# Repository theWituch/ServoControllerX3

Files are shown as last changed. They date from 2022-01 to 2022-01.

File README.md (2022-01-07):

# SCX3
3 Axis **Open-Loop STEP/DIR Position Control** to **Closed-Loop +/-10V Speed Control** Interface

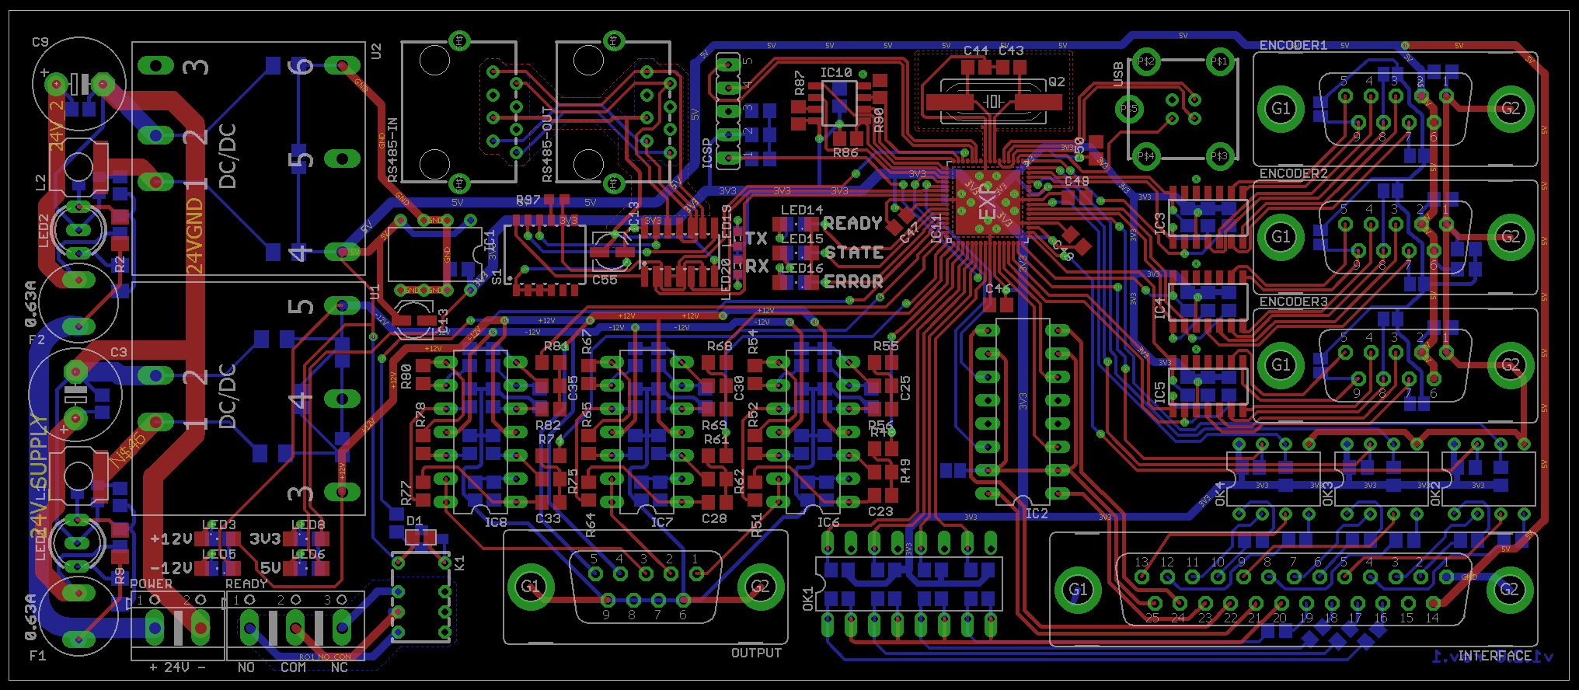
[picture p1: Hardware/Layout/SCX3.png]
PCB


## About
The system is an interface between two systemically incompatible types of control - open loop STEP/DIR in which there is no feedback, because it is open, and closed loop +/- 10V in which the DIRECT feedback is in the form of the axis position from a linear encoder for a linear axis or rotary for rotary axes (e.g. rotary table).

## How it works

The open-loop CNC controller has no coupling, it only sends STEP/DIR signals and waits for the movement to be performed, e.g. by a stepper motor or servo drive with a STEP / DIR input. This solution is nice and cheap, but it brings with it problems such as the lack of feedback on whether the move was actually made.

Of course, it is possible to detect, for example, in self-drives, the lack of rotation of the motor shaft, but the rotation of the motor does not have to mean the axis shift (failure).

In addition, the entire kinematic chain, which has its efficiency, causes that the positioning from the motor axis is not accurately reflected at the end of the chain (on the machine table).

## Project assumptions

The assumptions for the system were such as to:
* fit on one board for three axes of the machine
* reduce noise on the analog outputs +/- 10V
* ensure internal distribution of the necessary voltages for the system (uC, outputs +/- 10V) and connected encoders from the power supply 12-24VDC
* add a readiness relay (not a safe output, only OK status signaling, as in the servers it was supposed to cooperate with)
* increase the uC computing power
* increase the capacity of the encoder inputs
* integrate the RS232 interface in the system
* and adjust the shape of the board to the format that allows it to be reasonably mounted, e.g. on a DIN rail.

## Progress

The project, due to the fact that while writing the firmware, I encountered a bug with the EEPROM memory built into the uC, it got stuck for a good two years.

Problem: https://www.microchip.com/forums/m1043135.aspx  
Solution: https://www.microchip.com/forums/FindPost/1064146

## Versions

See version description to get more detailed informations.

* [version 1.2.0](V1.2.0.md)
* [version 1.1.0](V1.1.0.md)
* [version 1.0.0](V1.0.0.md)

## License

Whole SCX3 project follow [CC-BY-NC-SA-4.0 license](https://creativecommons.org/licenses/by-nc-sa/4.0/). Thus, project is freely available for academic purpose or individual research, but restricted for commecial use.

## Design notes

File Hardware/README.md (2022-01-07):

# SCX3 Hardware
3 Axis **Open-Loop STEP/DIR Position Control** to **Closed-Loop +/-10V Speed Control** Interface - Hardware

## About

The hardware for the SCX3 controller was developed using the EAGLE 7.7.0 environment.

## Status

The project has not been developed for a long time and the content of the repository has not been checked. Therefore, there is no guarantee that the project files will generate a PCB without any additional steps.

Additionally, this hardware version (1.2.0) has not been tested on the built prototype.

The only version tested on a prototype is 1.0.0 - which contained bugs that were fixed in later versions.

## License

SCX3 Hardware follow [CC-BY-NC-SA-4.0 license](LICENSE). Thus, those compounds are freely available for academic purpose or individual research, but restricted for commecial use.

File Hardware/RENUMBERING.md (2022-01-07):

# Don't renumber these!

POWER;READY;INTERFACE;ENCODER;OUTPUT;RS232;USB;ICSP

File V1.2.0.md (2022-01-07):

# SCX3 v1.2.0

## Layout

PCB

## Hardware changes

The most important hardware change is the addition of an RS-485 interface with two RJ-45 connectors instead of the RS-232 interface. RS-485 has better properties allowing it to work in more difficult conditions. The parameters of the RS-485 interface can be hardware controlled by means of S1 switches.

The entire power section was also rebuilt by changing the +/- 12V converter from Traco to Aimtec. The converters now have individual 24V power circuits with a separate fuse and a LED indicator for the burnout status.

## Firmware changes

The software has undergone general cleanup. The layout of the program has been changed, although its functionality has remained almost completely unchanged.

The most important change was the implementation of the MODBUS protocol which replaced text communication over RS-232.

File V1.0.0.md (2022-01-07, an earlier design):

# SCX3 v1.0.0

First version of board, with working prototype built.

## Layout

PCB

## Layout elements

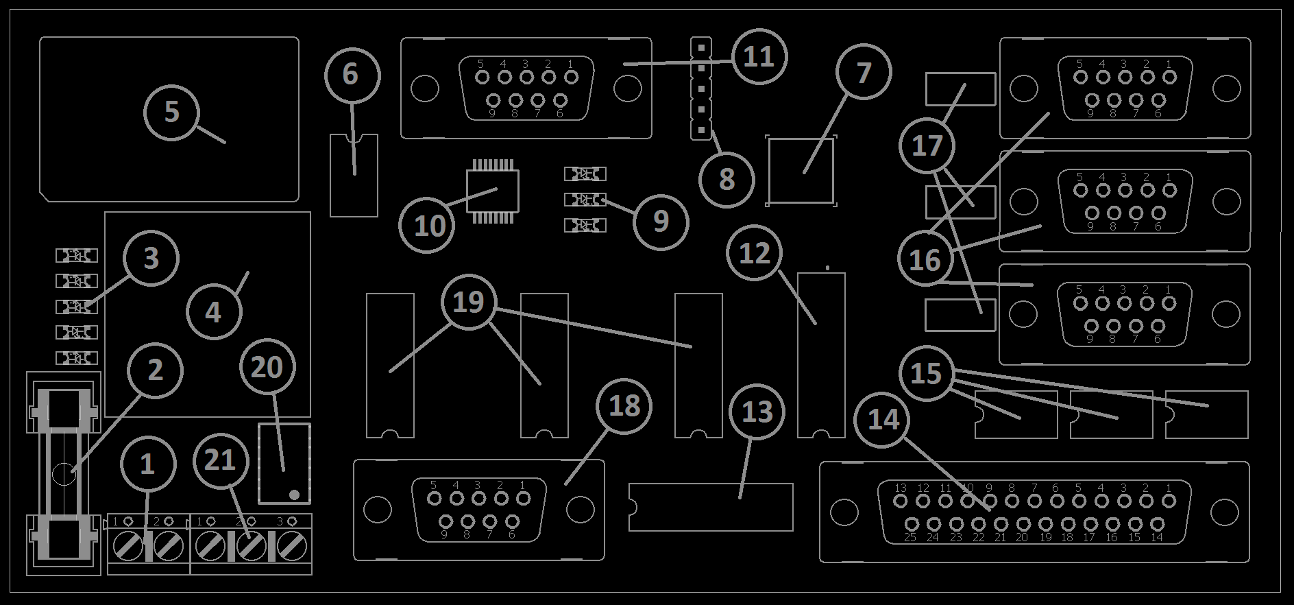
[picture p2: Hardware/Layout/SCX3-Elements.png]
PCB elements


     1 - 12-24 VDC power connector (+ VDC, GND)
     2 - fuse socket
     3 - 12-24VDC, +/- 12VDC, 5VDC, 3V3DC voltage presence LEDs
     4 - DC / DC converter 12-24VDC to 5VDC
     5 - DC / DC converter 12-24VDC to +/- 12VDC
     6 - LDO 5VDC to 3V3DC stabilizer
     7 - PIC32 microcontroller
     8 - ICSP connector for programming the microcontroller
     9 - device status indicator LEDs
    10 - RS232 transceiver
    11 - DB9 RS232 connector
    12 - DO transistorized digital output driver
    13 - DI digital input optocouplers
    14 - DB25 interface for STEP / DIR, DI, DO "INTERFACE" signals
    15 - STEP / DIR input optocouplers
    16 - DB9 connectors for encoder inputs "ENCODER (1,2,3)"
    17 - optocouplers for encoder inputs
    18 - DB9 "OUTPUT" connector of symmetrical +/- 10VDC outputs
    19 - symmetrical +/- 10VDC operational amplifiers
    20 - "READY" system readiness circuit relay
    21 - 3-pin connector of the "READY" relay (NO, COM, NC contacts)

## Prototype

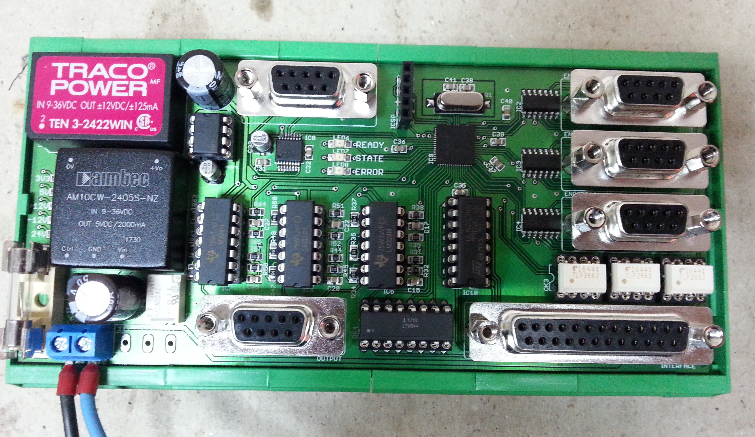
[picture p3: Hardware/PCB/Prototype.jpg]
PCB prototype

*There are no '21' connector soldered.*

The prototype showed design errors (wrongly arranged descriptions, swapped pin in the ENCODER1 encoder plug and badly designed READY relay power supply). However, this was not an obstacle to testing and developing the firmware.

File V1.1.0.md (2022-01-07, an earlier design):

# SCX3 v1.1.0

First version of board, with working prototype built.

## Layout

PCB

## Hardware changes

- External SPI EEPROM memory added
- K1 (READY) relay has been changed to 5V supply type due to separation of ground from supply voltage.
- RS232 interface socket has been changed from DB9 plug to RJ9
- The +/- 12V voltage lead has been added to the OUTPUT connector

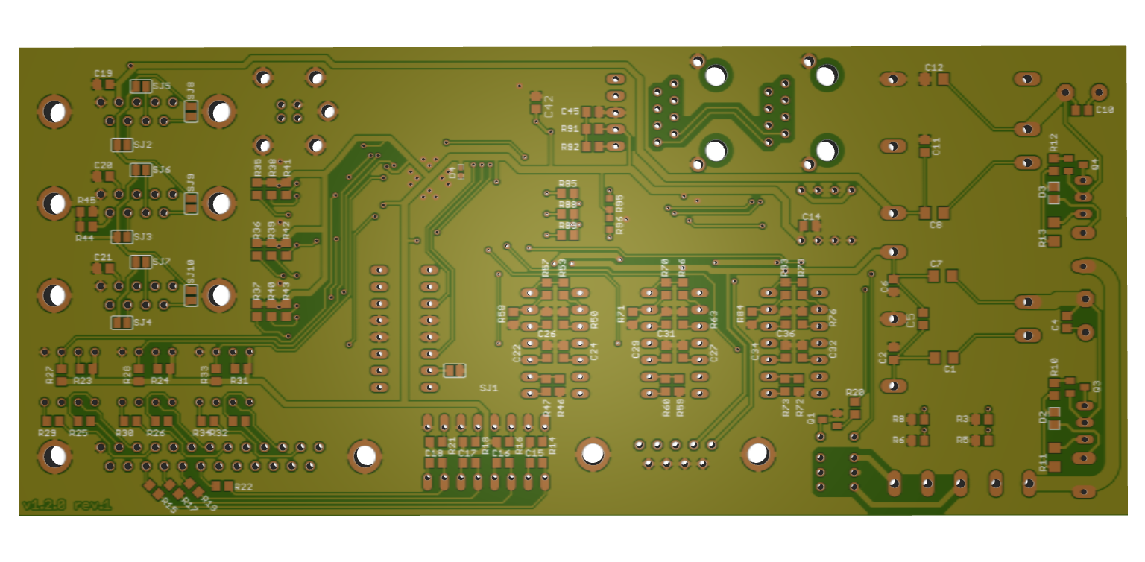
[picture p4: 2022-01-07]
Hardware/Layout/SCX3-3D_Bottom.png

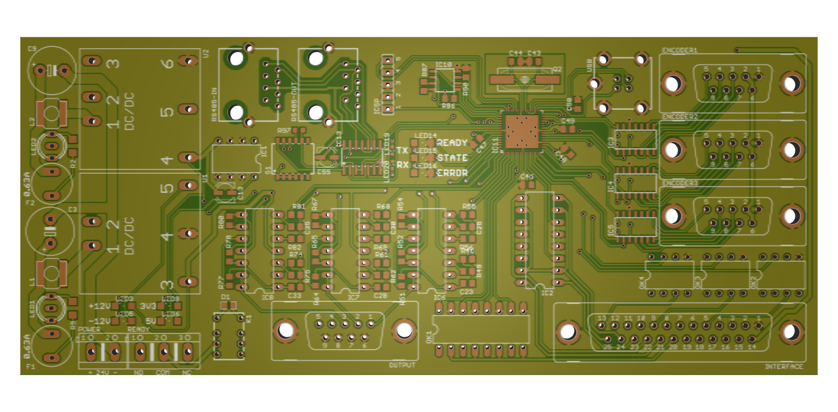
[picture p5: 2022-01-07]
Hardware/Layout/SCX3-3D_Top.png

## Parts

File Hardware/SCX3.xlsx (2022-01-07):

NO | Qty | Device | Value | Package | Parts | Description | POSIADANE | ZAMOWIENIE
1 | 1 | 1N4148SMD-0805 | 1N4148SMD-0805 | D0805 | D1 | DIODE
2 | 1 | AK500/2 | 12/24V_CON | AK500/2 | POWER | CONNECTOR
3 | 1 | AK500/3 | READY | AK500/3 | READY | CONNECTOR
4 | 1 | AM10CW-2405S-NZ | AM10CW-2405S-NZ | AM10CW-NZ | U1 | 10 Watt | 2A | DC-DC Converter
5 | 1 | BC848SMD | BC848SMD | SOT23 | Q4 | NPN Transistor
6 | 14 | C-EUC0805 | 100n | C0805 | C29, C30, C31, C32, C34, C35, C36, C37, C39, C40, C42, C43, C44, C45 | CAPACITOR
7 | 9 | C-EUC0805 | 33n | C0805 | C14, C16, C18, C19, C21, C23, C24, C26, C28 | CAPACITOR
8 | 6 | C-EUC0805 | 10n | C0805 | C15, C17, C20, C22, C25, C27 | CAPACITOR
9 | 5 | C-EUC0805 | 10uF | C0805 | C3, C10, C11, C12, C13 | CAPACITOR
10 | 2 | C-EUC0805 | 1nF/2KV | C0805 | C4, C8 | CAPACITOR
11 | 2 | C-EUC0805 | 27p | C0805 | C38, C41 | CAPACITOR
12 | 3 | C-EUC0805 | 1uF | C0805 | C2, C5, C7 | CAPACITOR
13 | 1 | CPOL-EUE5-10.5 | 200uF | E5-10,5 | C6 | POLARIZED CAPACITOR
14 | 1 | CPOL-EUE5-10.5 | 330uF | E5-10,5 | C1 | POLARIZED CAPACITOR
15 | 1 | CPOL-EUUD-4X5,8 | 100n | UD-4X5,8 | C33 | POLARIZED CAPACITOR
16 | 1 | CPOL-EUUD-4X5,8 | 10uF | UD-4X5,8 | C9 | POLARIZED CAPACITOR
17 | 1 | CRYSTALSM49 | 20MHz 18pF | SM49 | Q1 | CRYSTAL
18 | 1 | DJNR6028--S | 4,7uH | DJNR6028 | L1 | INDUCTOR
19 | 5 | F09VP |  | F09VP | ENCODER1, ENCODER2, ENCODER3, OUTPUT, RS-232 | SUB-D
20 | 1 | F25VP |  | F25VP | INTERFACE | SUB-D
21 | 1 | G6K-2P-Y | G6K-2P-Y | G6K-2P-Y | K1 | Low Signal Relay
22 | 1 | JP5E | ICSP | JP5 | ICSP | JUMPER
23 | 3 | LEDSML1206 | LED +12V, -12V, 5V | SML1206 | LED2, LED3, LED4 | Green LED 20mA 2,5V
24 | 3 | LEDSML1206 | LED 24V, 3V3, READY | SML1206 | LED1, LED5, LED6 | Green LED 10mA 2,5V
25 | 1 | LEDSML1206 | LED ERROR | SML1206 | LED8 | Red LED 10mA 2,5V
26 | 1 | LEDSML1206 | LED STATE | SML1206 | LED7 | Orange LED 10mA 2,5V
27 | 3 | LM324N | LM324N | DIL14 | IC5, IC6, IC7 | OP AMP
28 | 3 | LM339D | LM339D | SO14 | IC2, IC3, IC4 | Low Power Low Offset Voltage Quad Comparators
29 | 1 | LTV844 | LTV844 | DIL16 | OK4 | SHARP OPTO COUPLER
30 | 1 | MAX3221CAE | MAX3221CAE | SSOP16 | IC8 | RS-232 Transceivers with AutoShutdown
31 | 1 | MAX604 | MAX604 | DIL08 | IC1 | LDO VOLTAGE REGULATOR
32 | 1 | PIC32MK1024MCF064 | PIC32 | QFN64-9X9 | IC9 | PIC32 MICROCONTROLLER
33 | 21 | R-EU_R0805 | 22K | R0805 | R30, R31, R34, R35, R36, R38, R40, R43, R44, R47, R48, R49, R51, R53, R56, R57, R60, R61, R62, R64, R66 | RESISTOR
34 | 20 | R-EU_R0805 | 4K7 | R0805 | R6, R7, R10, R11, R14, R16, R18, R19, R20, R21, R22, R23, R24, R25, R26, R73, R77, R81, R82, R88 | RESISTOR
35 | 12 | R-EU_R0805 | 47K | R0805 | R29, R33, R37, R41, R42, R46, R50, R54, R55, R59, R63, R67 | RESISTOR
36 | 8 | R-EU_R0805 | 470 | R0805 | R2, R3, R8, R9, R12, R13, R15, R17 | RESISTOR
37 | 7 | R-EU_R0805 | 10K | R0805 | R32, R39, R45, R52, R58, R65, R71 | RESISTOR
38 | 6 | R-EU_R0805 | 1K | R0805 | R28, R72, R74, R79, R84, R89 | RESISTOR
39 | 4 | R-EU_R0805 | 100 | R0805 | R5, R68, R69, R70 | RESISTOR
40 | 1 | R-EU_R0805 | 130 | R0805 | R4 | RESISTOR
41 | 1 | R-EU_R0805 | 330 | R0805 | R27 | RESISTOR
42 | 1 | R-EU_R1206 | 2K2 | R1206 | R1 | RESISTOR
43 | 1 | SH22,5 | 3A | SH22,5 | F1 | FUSE HOLDER grid 22,5 mm
44 | 1 | TEN3-2422WIN | TEN3-2422WIN | TEN3-WIN | U2 | 3W | DC/DC Converter
45 | 3 | TLP2662F | TLP2662F | DIL08 | OK1, OK2, OK3 | 2 GATE FAST OPTO COUPLER
46 | 1 | ULN2074BN | ULN2074BN | DIL16 | IC10 | DRIVER ARRAY
47
48
49
50

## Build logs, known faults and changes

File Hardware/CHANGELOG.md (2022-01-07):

# 1.2.0
- the dimensions of the plate have been corrected to 159x73mm (from 157x72mm)
- PCB dimensions have been corrected to 170x73mm (from 159x72mm), adding one housing module
- IC3-5 and IC6-8 have been relocated
- individual voltage fuses for DC / DC converters have been added with LEDs indicating burnout
- the USB interface has been implemented
- RX / TX signaling diodes for communication have been added
- an RS-485 interface with two RJ-45 sockets was implemented instead of the RS-232
- changed the + -12V converter type from Traco to Aimtec
- a diode has been added to protect the 3V3 power supply against overvoltage

# 1.1.0
- the error of connecting the encoder interface ENCODER1 has been corrected - the connection of the CH1_QE_x leads has been changed:
CH1_QE_A> IC9.30
CH1_QE_B> IC9.33
CH1_QE_I> IC9.31
- fixed error of connecting (no ground) relay output RO1 - change to 5V power supply
- the resistance values of the resistors R27 and R28 have been changed
R27> 1K ohm
228> 470 ohms
- the bug with the description of the R27 and R28 resistors has been corrected
- added external SPI EEPROM memory
- RS232 interface socket has been changed from DB9 plug to RJ9
- the position of the 24 / + - 12V converter and accessories has been corrected
- the position of the 5 / 3.3V converter and accessories has been corrected
- the +/- 12V voltage lead has been added to the OUTPUT connector

# 1.0.0
- the first version of the layout

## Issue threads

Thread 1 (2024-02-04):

If use pwm10v it suport for Axis Mach3

artayasa, 2024-02-04:
Hi sir.
I interest with your project i have ac servo snayo denki 200v, with 2000ppr. It posoble to use ypur hardware and frimeware? I want to used mach3

theWituch, 2024-02-16:
Hi,
you are free to use this design for personal purposes if you do not intend to commercially offer this layout for sale.
The project is unfinished (firmware), so if you want it as it is, it will be difficult to make it work - anyway fell free to create PR with updates ;)

artayasa, 2024-02-16:
> Hi, you are free to use this design for personal purposes if you do not intend to commercially offer this layout for sale. The project is unfinished (firmware), so if you want it as it is, it will be difficult to make it work - anyway fell free to create PR with updates ;)

So it not suport for step/dir but closeloop with encorder 2000ppr??
And posible to make for stm32f401??

theWituch, 2024-02-22:
It support STEP/DIR input from controller (eg. Mach3) - also this board has capability to recieve command also by RS-485 port (need firmware development).

Its designed to recieve motion commands (especially STEP/DIR) and control closed-loop +/-10V  speed-control servo. Any TTL encoder supported (2000ppr will work excellent).

Read README for more informations.
But remember - project is unfinished ;)

artayasa, 2024-02-22:
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

This is for bldc/pmsm motor control right sir??

artayasa, 2024-07-18:
> It is as described: 3 Axis Open-Loop _STEP/DIR Position Control_ to Closed-Loop _+/-10V Speed Control_ **Interface**

So its mean posoble to used for cnc?? Because speed control?? And cnc is position control right??

theWituch, 2024-07-25:
Of course, it is designed primarily for use in CNC machines :)

I'm afraid you don't understand the purpose of SCX3. It is primarily a controller, not an motor driver like servo driver (not have a power amplifier). It must cooperate as interface between NC controller and motor driver.

Here is simple [diagram of major usage of SCX3](https://www.plantuml.com/plantuml/png/PP11Ru9048Nl-oicN1kgoAs7HeCqDH4nW4qJus4BMzm8EsHPxA7fV--mc0RBRU1xUU-3PMkuDbrTCTPUf6guvZKeB4Gh6l3cSyQO5hdXggm4fC6x3zyCe45jf09diyl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).

artayasa, 2024-07-25:
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

Owhh i got it now. Do u have idea for encorder actual position?? Must be linier encorder???
And if like that its mean any servo suport speed control 0-10v are posible right???
So i will planing to used any servo drive or vesc ( vesc suport speed control but as i know only 0-5v) it posible to make it 0-5v??

theWituch, 2024-08-06:
No, linear encoder is not neccesary but best - you can use any encoder which will be used as "real position" feedback.
In fact, the motor encoder can also be used to measure the real position, but the mechanical system of the axis introduces an error and then such positioning is worse by a few micrometers or more.

Yes, any servo which accept analog input as control signal will work with SCX3.

Yes, you can make it 5V in two ways - one is to change values   of the appropriate resistors of analog output block (its harder) and second is to limit the maximum value for output in the firmware (easier and you can change it anytime by reflashing).

And again, as I mentioned previously you can use motor encoder as position feedback (connecting to SCX ENDODERx inputs) but you must change it in firmware to properly process motor encoder signal to position (very rarely one ppr is exactly a linear movement like 1um or 1mm because of mechanical system).

artayasa, 2024-08-06:
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

Oke thank u i gotit now, but the chip hard to find on my country, i think it is a stm32f407

theWituch, 2024-08-08:
I think best will be chip with hardware support for quadrature encoder like STM32F767ZI

artayasa, 2024-08-08:
> I think STM32f407 chip will be good as long have a hardware support for quadrature encoder.

Yes they have quadature suport, it just upload your code to stm32f407???

theWituch, 2024-08-12:
No, its not that simple. Firmware is written with Microchip libraries and for PIC32 uC registers. STM is quite different, so it must be adjusted. General firmware flow will work probably, but I didnt check how much work it needs.
And dont forget, the board must be changed too because STM32F407 has different package and pinout.

artayasa, 2024-08-13:
> No, its not that simple. Firmware is written with Microchip libraries and for PIC32 uC registers. STM is quite different, so it must be adjusted. General firmware flow will work probably, but I didnt check how much work it needs. And dont forget, the board must be changed too because STM32F407 has different package and pinout.

Oke sir, first must loking for pic32

theWituch, 2024-08-13:
Im not familiar with whole PIC32 family, so dont know. Just use PIC32MK1024MCF064 and you are ready to go with testing.
Which version of SCX3 you would use? I reccomend to start with latest [1.2.0](https://github.com/theWituch/ServoControllerX3/blob/master/V1.2.0.md)

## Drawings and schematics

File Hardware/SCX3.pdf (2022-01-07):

24V_2 | + + | +
Arkusz: 1/7 ABCD | 1 | 2 | 3 | 4 | 5 | 6 | ABCD 1 | 2 | 3 | 4 | 5 | 6

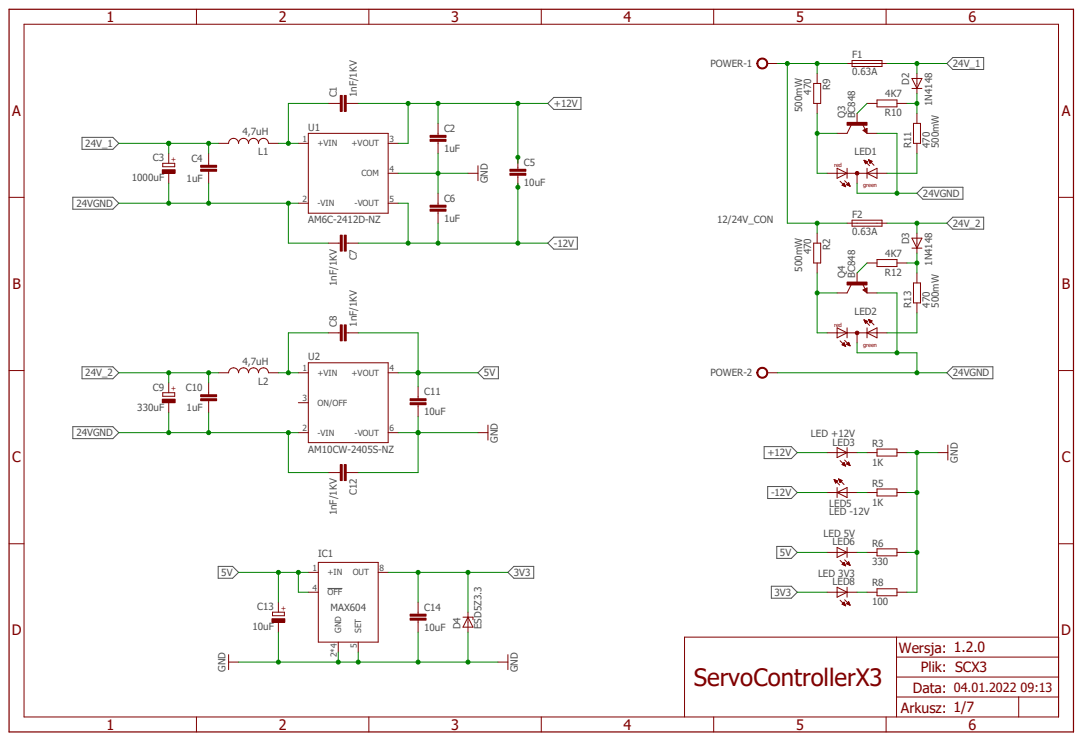
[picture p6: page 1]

# GND ⁴K7

Arkusz: 2/7 ABCD | 1 | 2 | 3 | 4 | 5 | 6 | ABCD 1 | 2 | 3 | 4 | 5 | 6

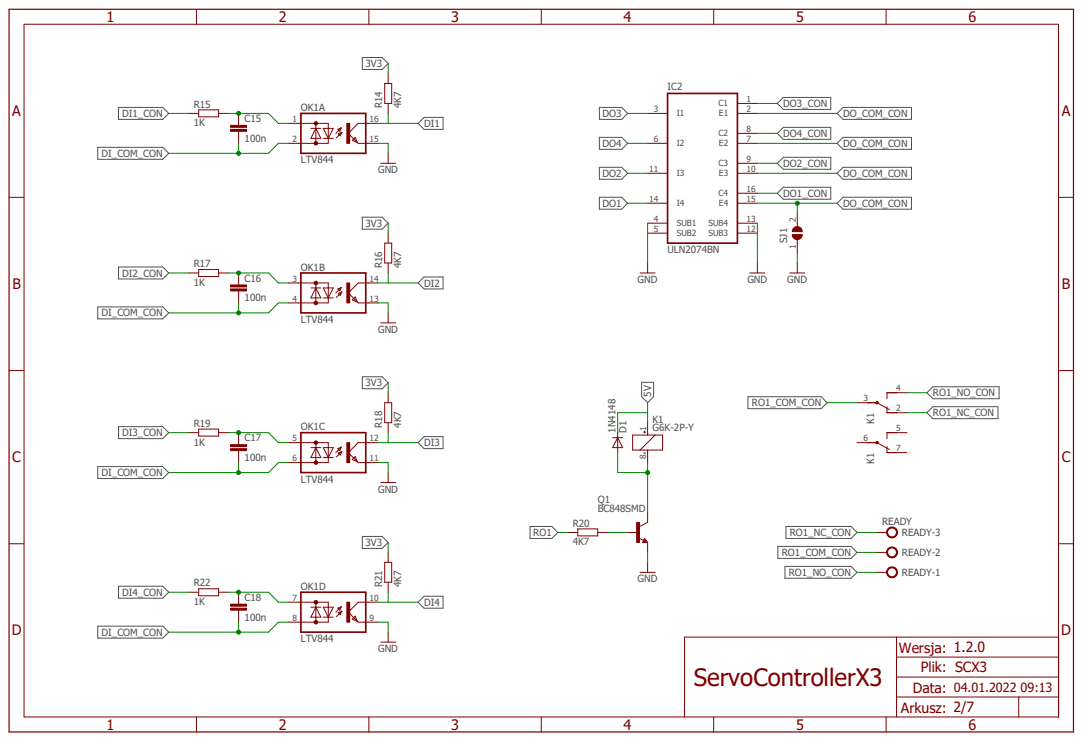
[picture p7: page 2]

Arkusz: 3/7 ABCD | 1 | 2 | 3 | 4 | 5 | 6 | ABCD 1 | 2 | 3 | 4 | 5 | 6

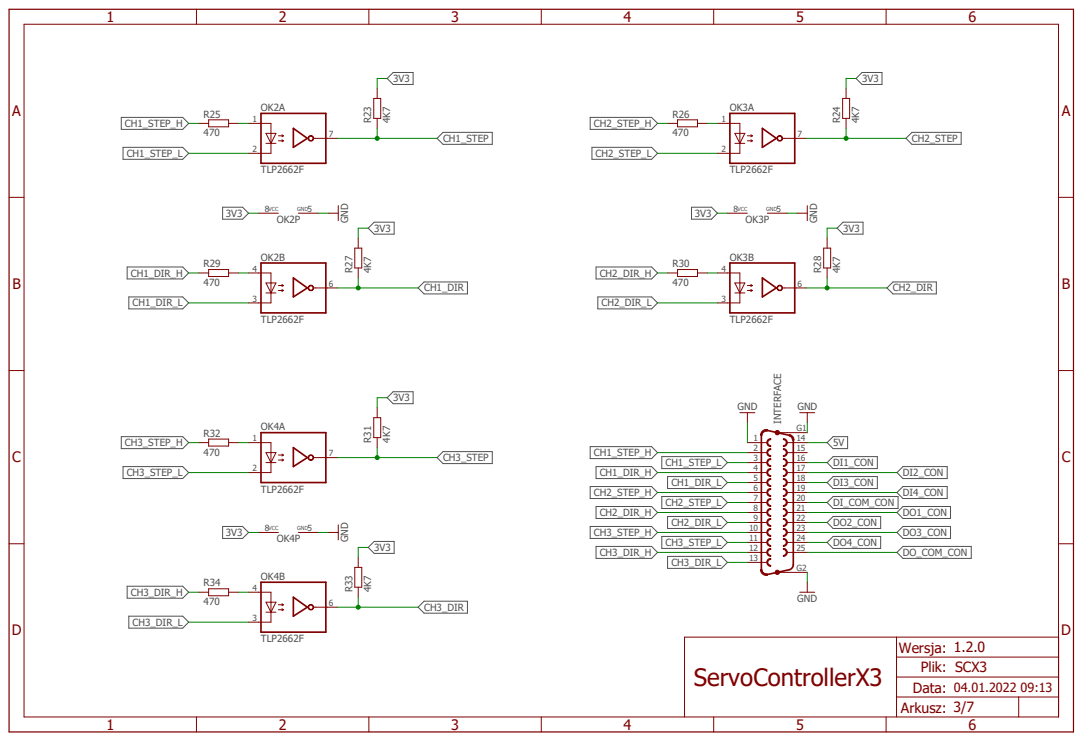
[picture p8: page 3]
TLP2662F; 470 4K7 4K7 GND; GND; R²³ R²⁷; VCC; R²⁴ R²⁸; R³¹ R³³; G2 INTERFACE; CH3_STEP; CH3_DIR; CH3_STEP_H; CH3_STEP_L; CH3_DIR_H; CH3_DIR_L; CH1_STEP_H; CH1_STEP_L; CH1_STEP; CH1_DIR_H; CH1_DIR_L; CH1_DIR; CH2_STEP_H; CH2_STEP_L; CH2_STEP; CH2_DIR; CH2_DIR_H; CH2_DIR_L; DO2_CON; DO1_CON; DI_COM_CON; DI4_CON; DI3_CON; DI2_CON; DI1_CON; DO3_CON; DO4_CON; DO_COM_CON; SCX3 04.01.2022 09:13; ServoControllerX3; Data:; Wersja: 1.2.0 Plik:

LM339D | GND
LM339D | GND

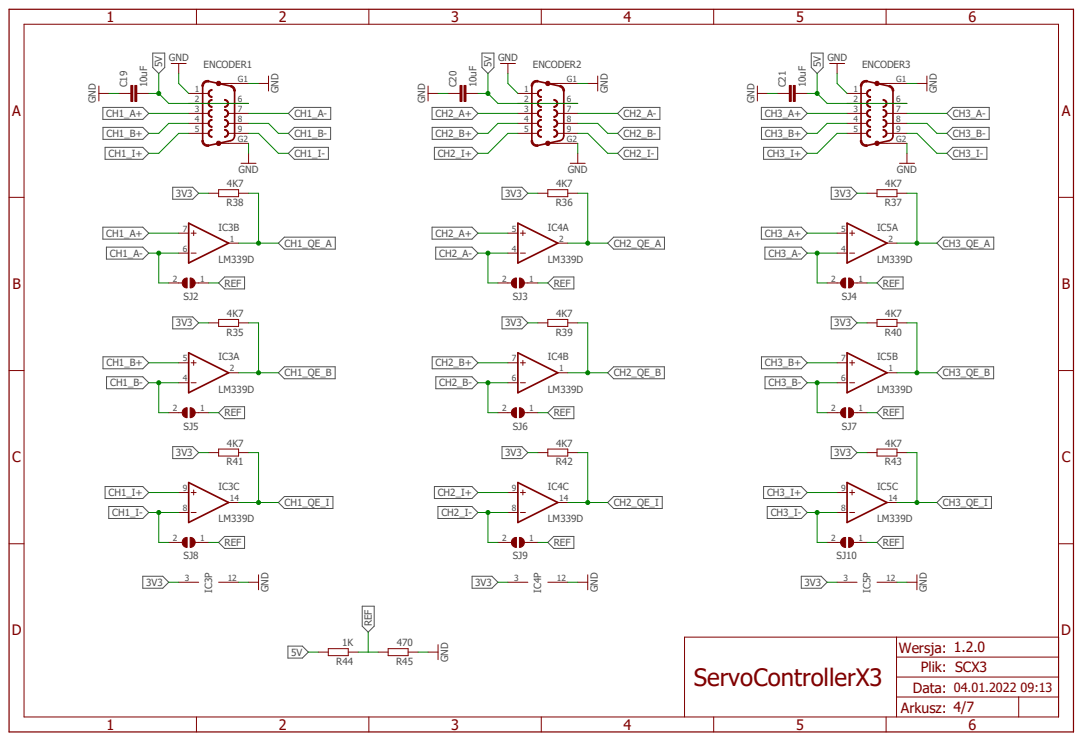
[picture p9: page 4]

C31 | C30 | 23 | 1

# R72 R⁸³

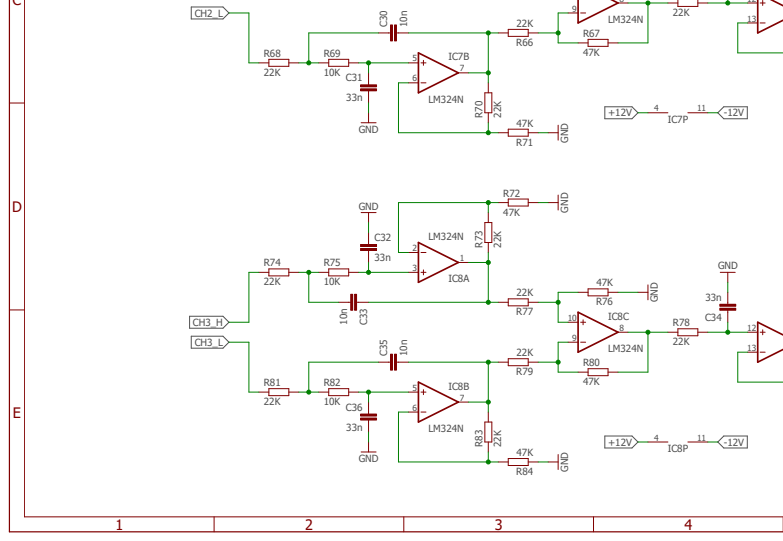
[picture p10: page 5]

C

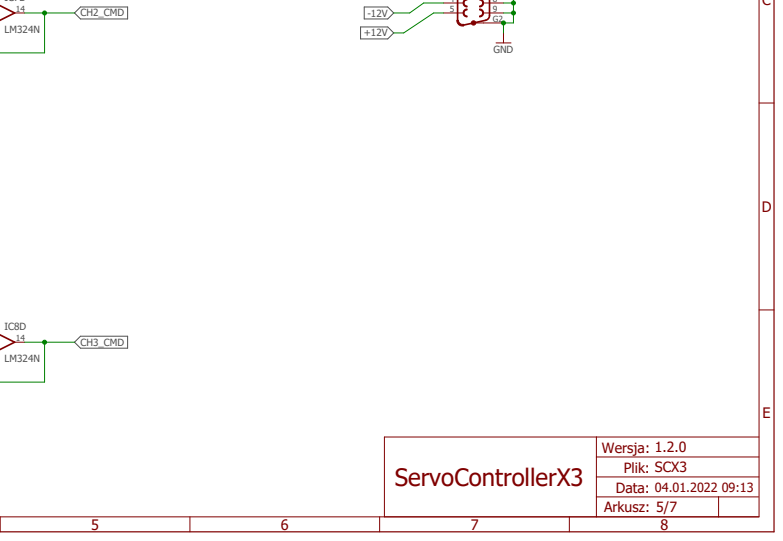
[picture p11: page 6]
GND; CH2_CMD; CH3_CMD; SCX3 04.01.2022 09:13; Data:; Wersja: Plik:; ServoControllerX3

Arkusz: 5/7

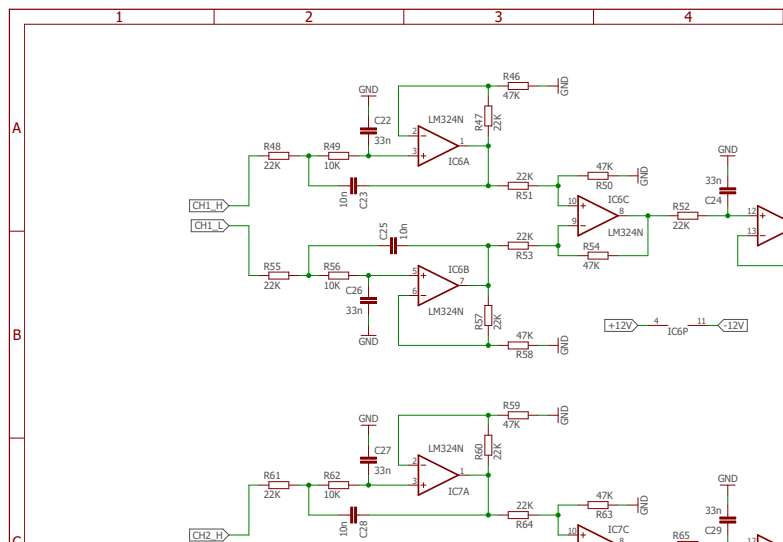
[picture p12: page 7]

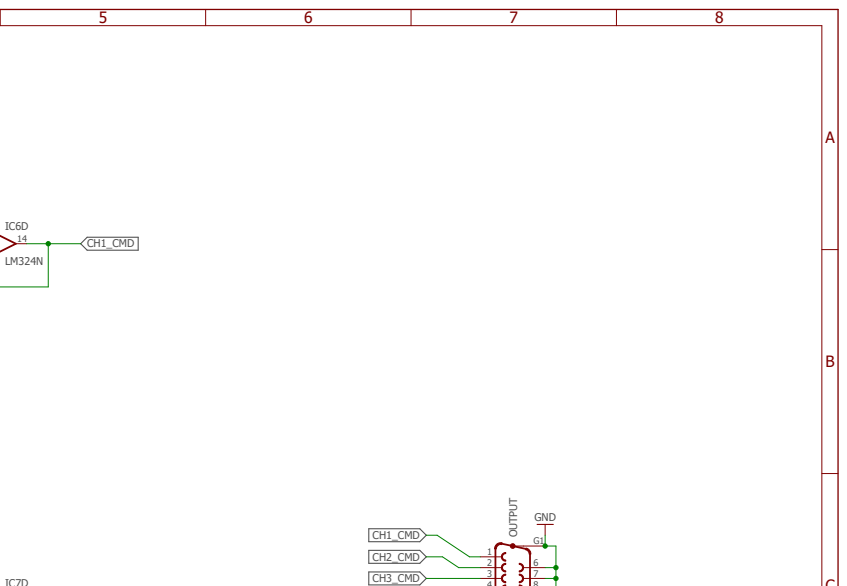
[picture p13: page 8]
GND; G1 OUTPUT; CH2_CMD; CH3_CMD; CH1_CMD; ABC 5

A

A

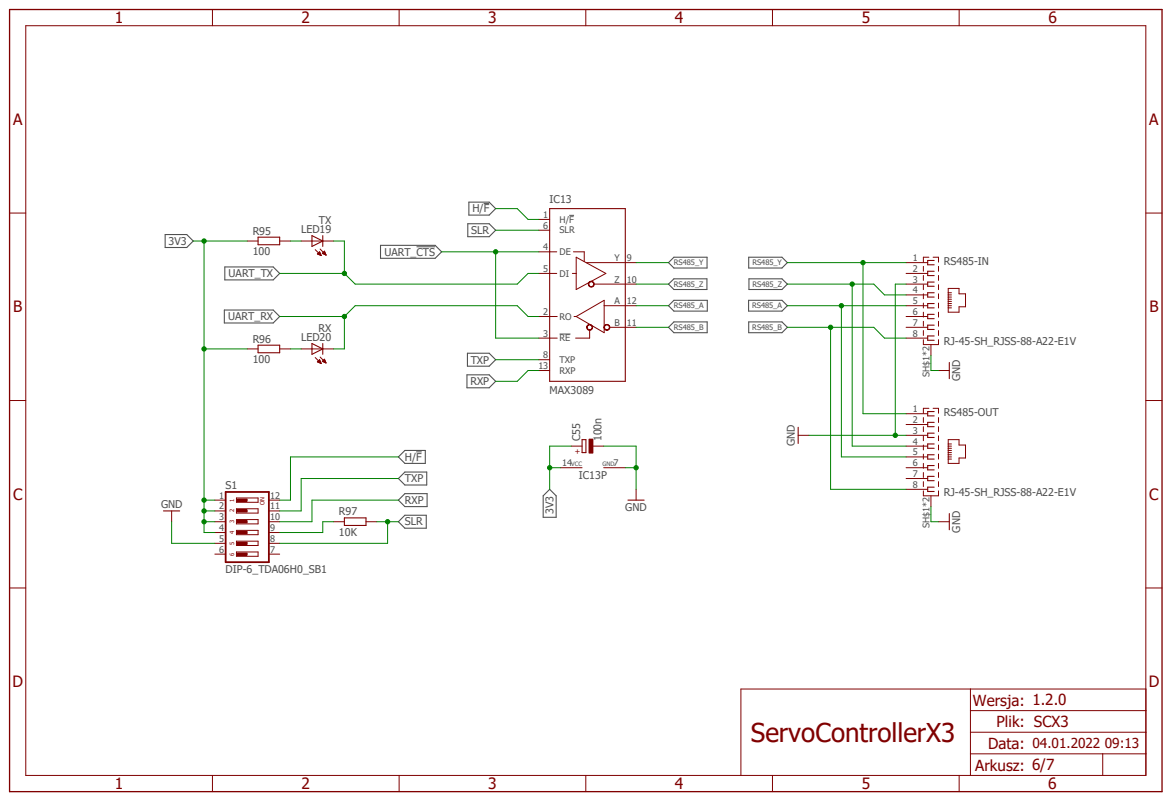
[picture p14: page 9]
GND; GND ¹⁰⁰n; MAX3089; RJ-45-SH_RJSS-88-A22-E1V; DIP-6_TDA06H0_SB1; LED19; LED20; TXP 8 RXP 13; SLR 6; VCC; RS485-OUT ¹ 2 3 4 5 6 7 8 SH$1*2; UART_TX; UART_RX; RXP; SLR; TXP; UART_CTS; SCX3 04.01.2022 09:13 Arkusz: 6/7; ServoControllerX3; Data:; Wersja: 1.2.0 Plik:

RJ-45-SH_RJSS-88-A22-E1V GND GND

3 | 10

PIC32MK1024MCF064

1K

100n

100n

100n ¹⁰⁰n GND | GND GND GND
AN19/CVD19/RPG6/PMPA5/RG6 4 AN18/CVD18/RPG7/PMPA4/RG7 5 AN17/CVD17/RPG8/PMPA3/RG8 6 MCLR 7
AN16/CVD16/RPG9/PMPA2/RG9 8 VSS 9*2
VDD 10
AN10/CVD10/RPA12/RA12 11
AN9/CVD9/RPA11/USBOEN1/RA11 12 OA2OUT/ANO/C2IN4-/C4IN3-/RPA0/RA0 13 OA2IN+/AN1/C2IN1+/RPA1/RA1 14 PGED3/VREF-/OA2IN-/AN2/C2IN1-/RPB0/CTED2/RB0 15 PGEC3/OA1OUT/VREF+/AN3/C1IN4-/C4IN2-/RPB1/CTED1/PMPA6/RB1 16

PGEC1/OA1IN+/AN4/C1IN1+/C1IN3-/C2IN3-/RPB2/RB2 17 PGED1/OA1IN-/AN5/CTCMP/C1IN1-/RTCC/RPB3/RB3 18
AVDD 19
AVSS 20
OA3OUT/AN6/CVD6/C3IN4-/C4IN1+/C4IN4-/RPC0/RC0 21 OA3IN-/AN7/CVD7/C3IN1-/C4IN1-/RPC1/PMPA7/RC1 22 OA3IN+/AN8/CVD8/C3IN1+/C3IN3-/RPC2/FLT3/PMPA13/RC2 23 AN11/CVD11/C1IN2-/FLT4/PMPA12/RC11 24
VSS 25
VDD 26
AN12/CVD12/C2IN2-/C5IN2-/FLT5/PMPA11/RE12 27 AN13/CVD13/C3IN2-/FLT6/PMPA10/RE13 28 AN14/CVD14/RPE14/FLT7/PMPA1/PSPA1/RE14 29 AN15/CVD15/RPE15/FLT8/PMPA0/PSPA0/RE15 30 TDI/DAC3/AN26/CVD26/RPA8/PMPA9/RA8 31 FLT15/RPB4/PMPA8/RB4 32

R92

C46

C49

C48 C45

3V3

3V3

3V3

DI4

DI1
DI2
DI3

CH1_QE_A

CH3_STEP
CH2_QE_I

CH3_QE_B

CH1_QE_I

CH2_QE_A

CH2_QE_B

CH3_QE_I

CH3_QE_A

DO3

CH2_DIR

CH3_DIR

CH1_STEP

CH1_DIR

CH2_STEP

DO4 CDE | 1 | 2 | 3 | 4

100n

100n | GND GND
OA5IN+/DAC1/AN24/CVD24/C5IN1+/C5IN3-/RPA4/T1CK/T1G/RA4 | 33 VBUS | 34 VUSB3V3 | 35 D- | 36 D+ | 37 VDD | 38 OSCI/CLKI/AN49/CVD49/RPC12/RC12 | 39 OSCO/CLKO/RPC15/RC15 | 40 VSS | 41 RD8 | 42 PGED2/RPB5/USBID1/RB5 | 43 PGEC2/RPB6/SCK2/PMPA15/RB6 | 44 DAC2/AN48/CVD48/RPC10/PMPA14/PSPCS/RC10 | 45 OA5OUT/AN25/CVD25/C5IN4-/RPB7/SCK1/INT0/RB7 | 46 SOSCI/RPC13/RC13 | 47 SOSCO/RPB8/RB8 | 48
TMS/OA5IN-/AN27/CVD27/C5IN1-/RPB9/RB9 | 49 TRCLK/RPC6/PWM6H/RC6 | 50 TRD0/RPC7/PWM12H/PWM6L/RC7 | 51 TRD1/RPC8/PWM5H/PMPWR/PSPWR/RC8 | 52 TRD2/RPD5/PWM12H/PMPRD/PSPRD/RD5 | 53 TRD3/RPD6/PWM12L/RD6 | 54 RPC9/PWM11H/PWM5L/RC9 | 55 VSS | 56 VDD | 57 RPF0/PWM11H/RF0 | 58 RPF1/PWM11L/RF1 | 59 RPB10/PWM3H/PMPD0/RB10 | 60 RPB11/PWM9H/PWM3L/PMPD1/RB11 | 61

C50

C47

3V3

3V3

PGED

PGEC

OSC1I

OSC1O

LED_ERROR

LED_READY

LED_STATE

UART_TX

UART_RX

RO1

DO2
DO1

CH1_QE_B

MWP

MSDI

MSDO

MSCK
MSS

USB_D+
USB_D-

VBUS

UART_CTS
UART_RTR

## SCX3

04.01.2022 09:13

## Arkusz: 7/7

5 | 6 | 7 | 8

C

D

E

## Data:

## Wersja: Plik:

1.2.0

# ServoControllerX3

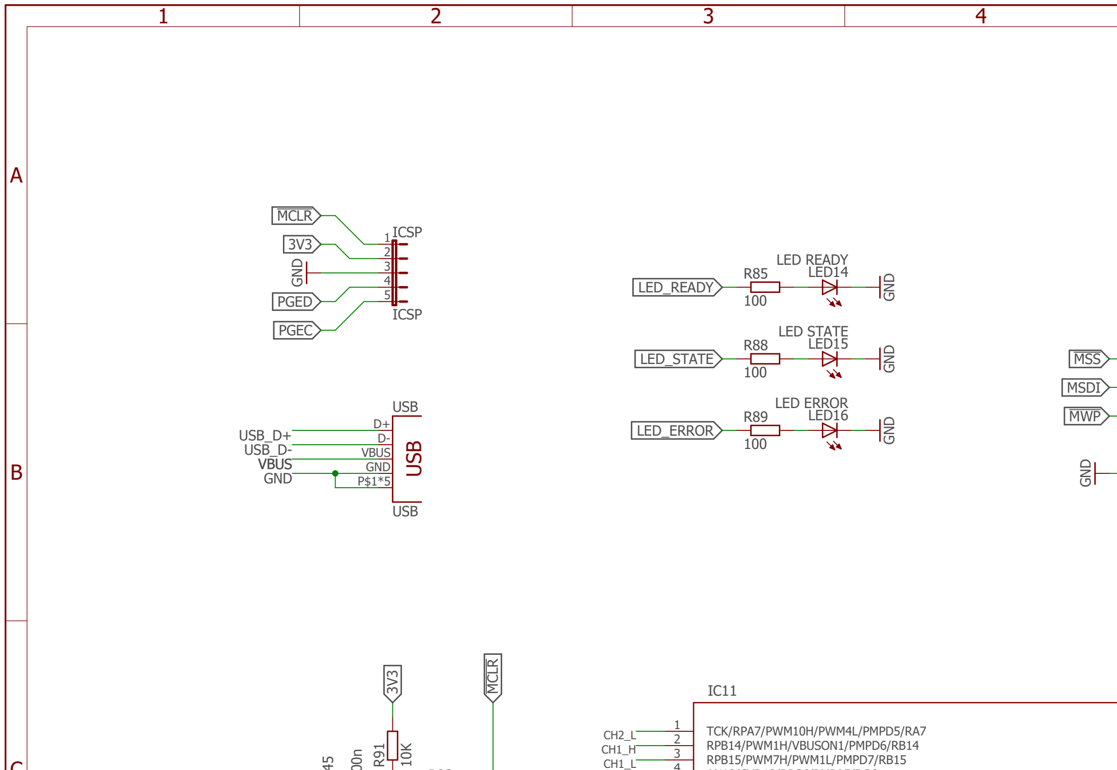
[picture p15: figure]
ICSP GND; LED READY; 100 GND; LED STATE 100 GND; LED ERROR; GND; USB; TCK/RPA7/PWM10H/PWM4L/PMPD5/RA7 1 RPB14/PWM1H/VBUSON1/PMPD6/RB14 2 RPB15/PWM7H/PWM1L/PMPD7/RB15 3; 4 R⁹¹; ICSP 1 2 3 4 5; LED14; LED15; LED16 D+; D- VBUS GND; MCLR; PGED; PGEC; LED_ERROR; LED_READY; LED_STATE; MWP; MSDI; MSS; USB_D+ USB_D- VBUS; 4 USB

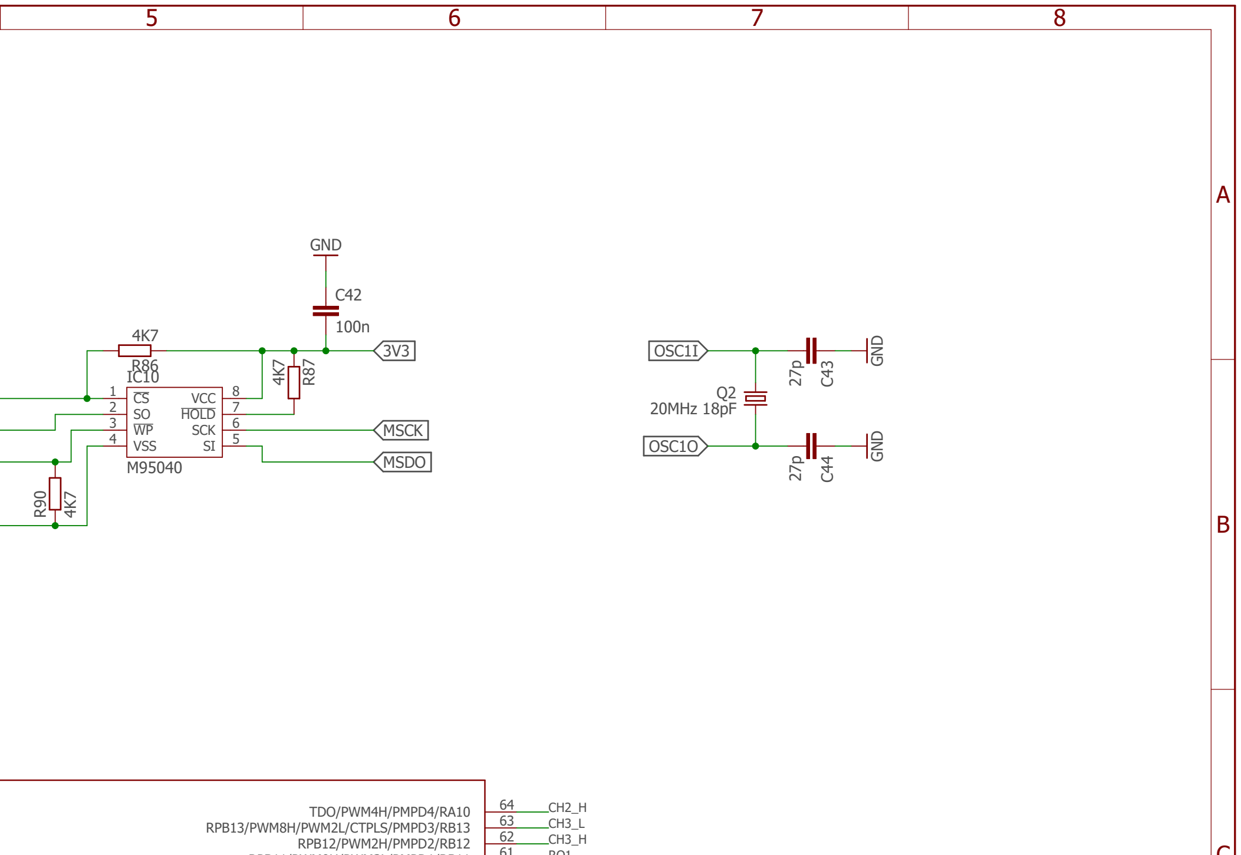
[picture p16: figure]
20MHz 18pF; GND GND; GND; 61 RPB12/PWM2H/PMPD2/RB12; 62 RPB13/PWM8H/PWM2L/CTPLS/PMPD3/RB13; 63 TDO/PWM4H/PMPD4/RA10; VSS 4; 5 SCK; 6 HOLD; 7 VCC; IC10 R⁹⁰; R⁸⁷; OSC1I; OSC1O; MSDO; MSCK

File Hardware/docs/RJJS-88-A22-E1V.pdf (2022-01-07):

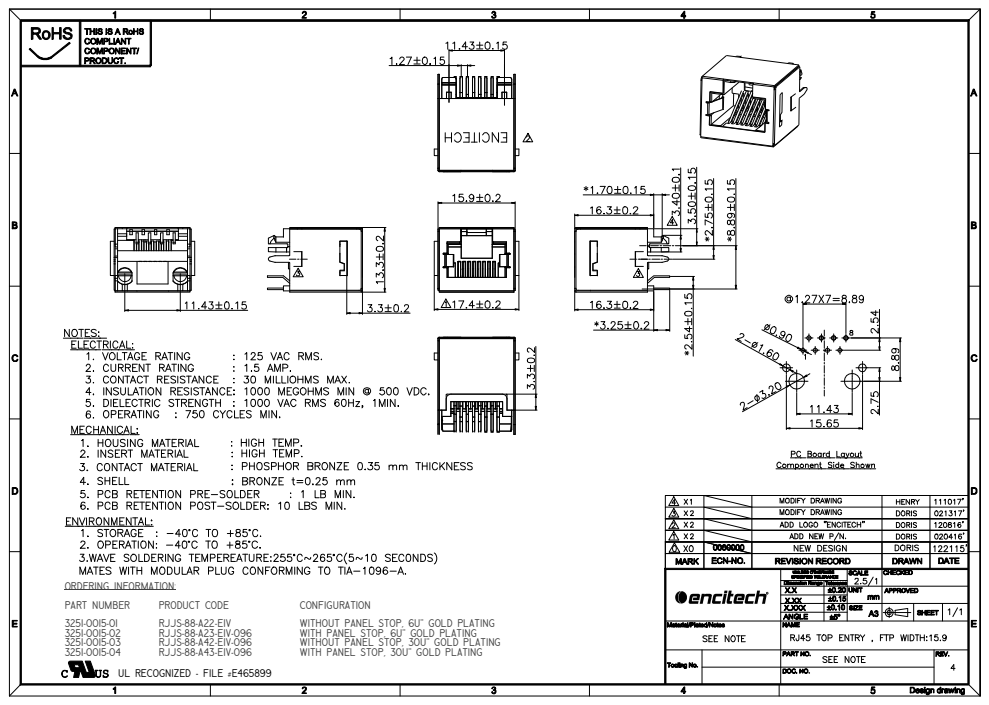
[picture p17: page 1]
0RDERING INF0RMATI0N:; PART NUMBER; PR0DUCT C0DE; C0NFIGURATI0N; RJJS-88-A22-E1V; WITH0UT PANEL ST0P, 6U" G0LD PLATING; RJJS-88-A23-E1V-096; WITH PANEL ST0P, 6U" G0LD PLATING; RJJS-88-A42-E1V-096; WITH0UT PANEL ST0P, 30U" G0LD PLATING; RJJS-88-A43-E1V-096; WITH PANEL ST0P, 30U" G0LD PLATING; UL REC0GNIZED - FILE #E465899

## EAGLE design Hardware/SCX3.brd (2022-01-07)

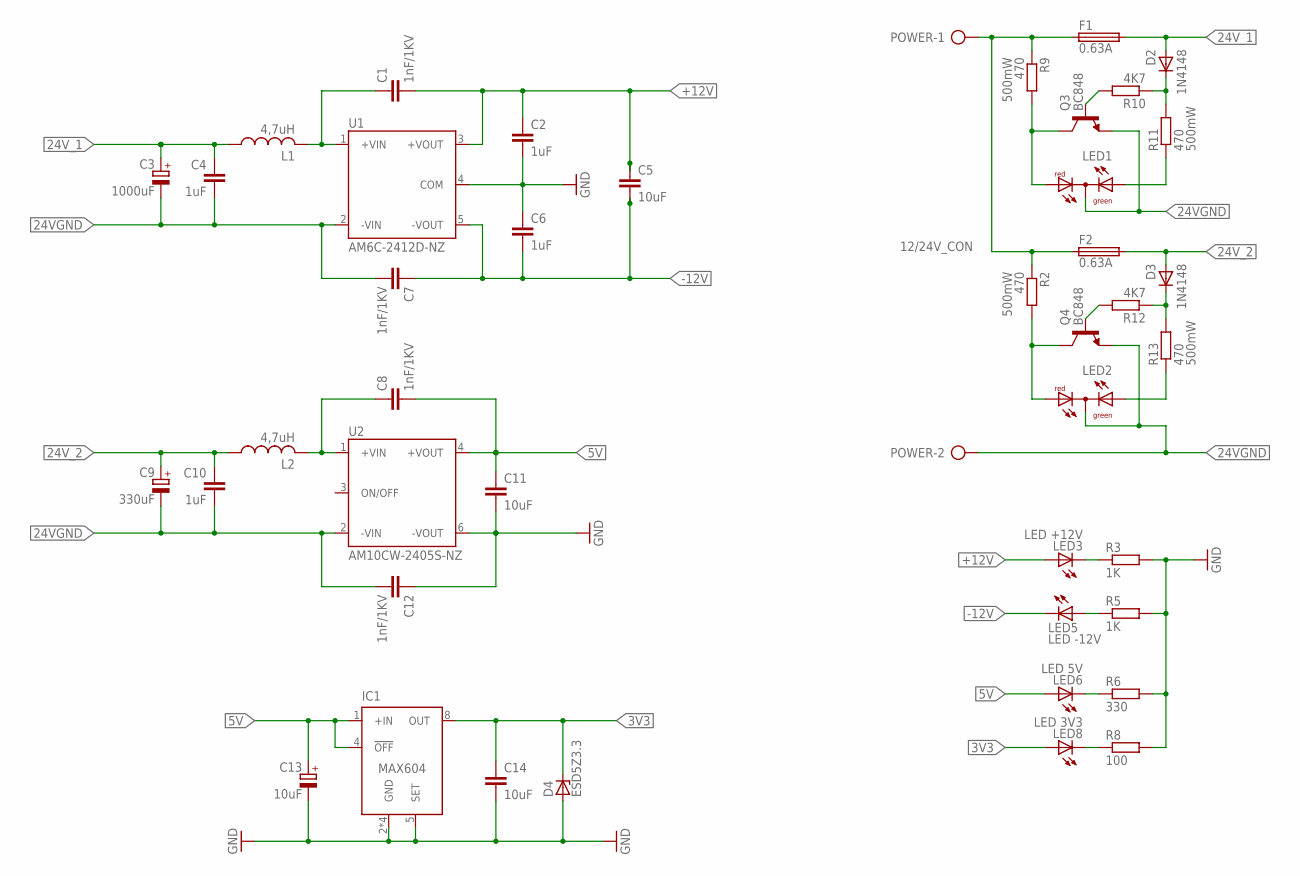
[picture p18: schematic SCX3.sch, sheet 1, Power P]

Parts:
C1, C7, C8, C12: 1nF/1KV; C1206
C2, C4, C6, C10: 1uF; C0805
C3: 1000uF; E5-10,5
C5, C11, C14: 10uF; C0805
C9: 330uF; E5-10,5
C13: 10uF; UD-4X5,8_NICHICON
D2, D3: 1N4148; D0805
D4: ESD5Z3.3; SOD523
F1, F2: 0.63A; TR5
IC1: MAX604; DIL08
L1, L2: 4,7uH; DJNR6028
LED1, LED2: DUOLED-RG-C; DUOLED-C-5MM
LED3: LED +12V; SML1206
LED5: LED -12V; SML1206
LED6: LED 5V; SML1206
LED8: LED 3V3; SML1206
POWER: 12/24V_CON; AK500/2
Q3, Q4: BC848; SOT23
R2, R9, R11, R13: 470; R1206
R3, R5: 1K; R0805
R6: 330; R0805
R8: 100; R0805
R10, R12: 4K7; R0805
U1: AM6C-2412D-NZ; AM6C
U2: AM10CW-2405S-NZ; AM10CW-NZ

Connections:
3V3: C14.1, D4.C, IC1.8 (OUT), LED8.A; also elsewhere on the board
5V: C8.2, C11.1, C13.+, IC1.1 (+IN), IC1.4 (!OFF), LED6.A, U2.4 (+VOUT); also elsewhere on the board
24VGND: C3.-, C4.2, C7.2, C9.-, C10.2, C12.2, LED1.C, LED2.C, POWER.2, Q3.2 (E), Q4.2 (E), U1.2 (-VIN), U2.2 (-VIN)
24V_1: C3.+, C4.1, D2.1 (A), F1.2, L1.A (1)
24V_2: C9.+, C10.1, D3.1 (A), F2.2, L2.A (1)
24V_SUPPLY: F1.1, F2.1, POWER.1, R2.1, R9.1
+12V: C1.2, C2.1, C5.1, LED3.A, U1.3 (+VOUT); also elsewhere on the board
-12V: C5.2, C6.2, C7.1, LED5.C, U1.5 (-VOUT); also elsewhere on the board
GND: C2.2, C6.1, C11.2, C12.1, C13.-, C14.2, D4.A, IC1.2 (GND), IC1.3 (GND), IC1.5 (SET), IC1.6 (GND), IC1.7 (GND), R3.2, R5.2, R6.2, R8.2, U1.4 (COM), U2.6 (-VOUT); also elsewhere on the board
unnamed: C8.1, L2.B (2), U2.1 (+VIN)
unnamed: C1.1, L1.B (2), U1.1 (+VIN)
unnamed: LED1.AR, Q3.3 (C), R9.2
unnamed: Q3.1 (B), R10.2
unnamed: LED3.C, R3.1
unnamed: LED1.AX (AG), R11.1
unnamed: D2.2 (C), R10.1, R11.2
unnamed: LED2.AR, Q4.3 (C), R2.2
unnamed: LED6.C, R6.1
unnamed: Q4.1 (B), R12.2
unnamed: LED2.AX (AG), R13.1
unnamed: LED8.C, R8.1
unnamed: LED5.A, R5.1
unnamed: D3.2 (C), R12.1, R13.2

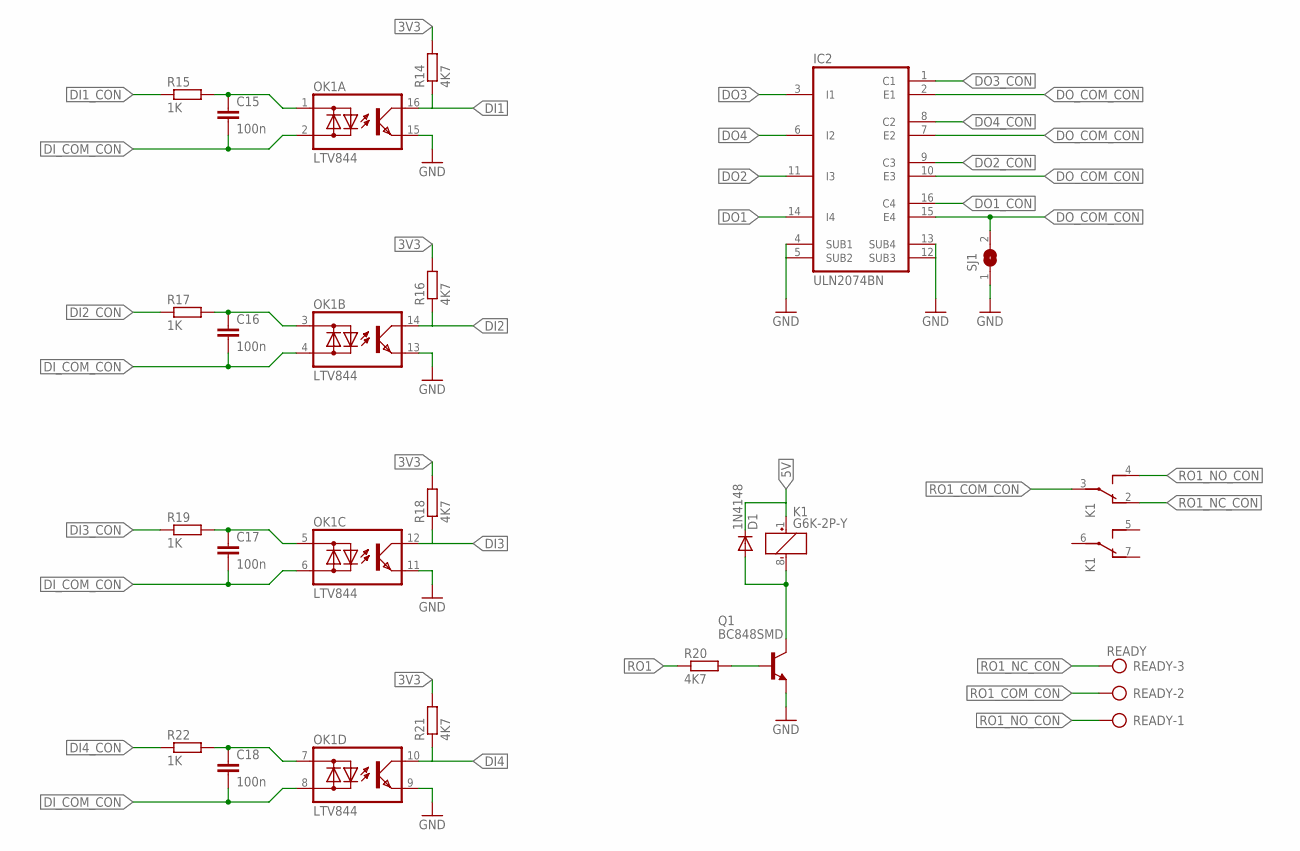
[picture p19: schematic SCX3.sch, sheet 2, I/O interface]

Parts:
C15, C16, C17, C18: 100n; C0805
D1: 1N4148; D0805
IC2: ULN2074BN; DIL16
K1: G6K-2P-Y
OK1: LTV844; DIL16
Q1: BC848SMD; SOT23
R14, R16, R18, R20, R21: 4K7; R0805
R15, R17, R19, R22: 1K; R0805
READY: READY; AK500/3
SJ1: SJ

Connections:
3V3: R14.2, R16.2, R18.2, R21.2; also elsewhere on the board
5V: D1.2 (C), K1.1 (+); also elsewhere on the board
DI1: OK1.16 (C), R14.1; also elsewhere on the board
DI1_CON: R15.1; also elsewhere on the board
DI2: OK1.14 (C), R16.1; also elsewhere on the board
DI2_CON: R17.1; also elsewhere on the board
DI3: OK1.12 (C), R18.1; also elsewhere on the board
DI3_CON: R19.1; also elsewhere on the board
DI4: OK1.10 (C), R21.1; also elsewhere on the board
DI4_CON: R22.1; also elsewhere on the board
DI_COM_CON: C15.2, C16.2, C17.2, C18.2, OK1.2 (AC2), OK1.4 (AC2), OK1.6 (AC2), OK1.8 (AC2); also elsewhere on the board
DO1: IC2.14 (I4); also elsewhere on the board
DO1_CON: IC2.16 (C4); also elsewhere on the board
DO2: IC2.11 (I3); also elsewhere on the board
DO2_CON: IC2.9 (C3); also elsewhere on the board
DO3: IC2.3 (I1); also elsewhere on the board
DO3_CON: IC2.1 (C1); also elsewhere on the board
DO4: IC2.6 (I2); also elsewhere on the board
DO4_CON: IC2.8 (C2); also elsewhere on the board
DO_COM_CON: IC2.2 (E1), IC2.7 (E2), IC2.10 (E3), IC2.15 (E4), SJ1.2; also elsewhere on the board
GND: IC2.4 (SUB1), IC2.5 (SUB2), IC2.12 (SUB3), IC2.13 (SUB4), OK1.9 (E), OK1.11 (E), OK1.13 (E), OK1.15 (E), Q1.2 (E), SJ1.1; also elsewhere on the board
unnamed: D1.1 (A), K1.8 (-), Q1.3 (C)
unnamed: C16.1, OK1.3 (AC1), R17.2
unnamed: Q1.1 (B), R20.2
unnamed: C17.1, OK1.5 (AC1), R19.2
unnamed: C18.1, OK1.7 (AC1), R22.2
unnamed: C15.1, OK1.1 (AC1), R15.2
RO1: R20.1; also elsewhere on the board
RO1_COM_CON: K1.3, READY.2
RO1_NC_CON: K1.2 (O), READY.3
RO1_NO_CON: K1.4 (S), READY.1

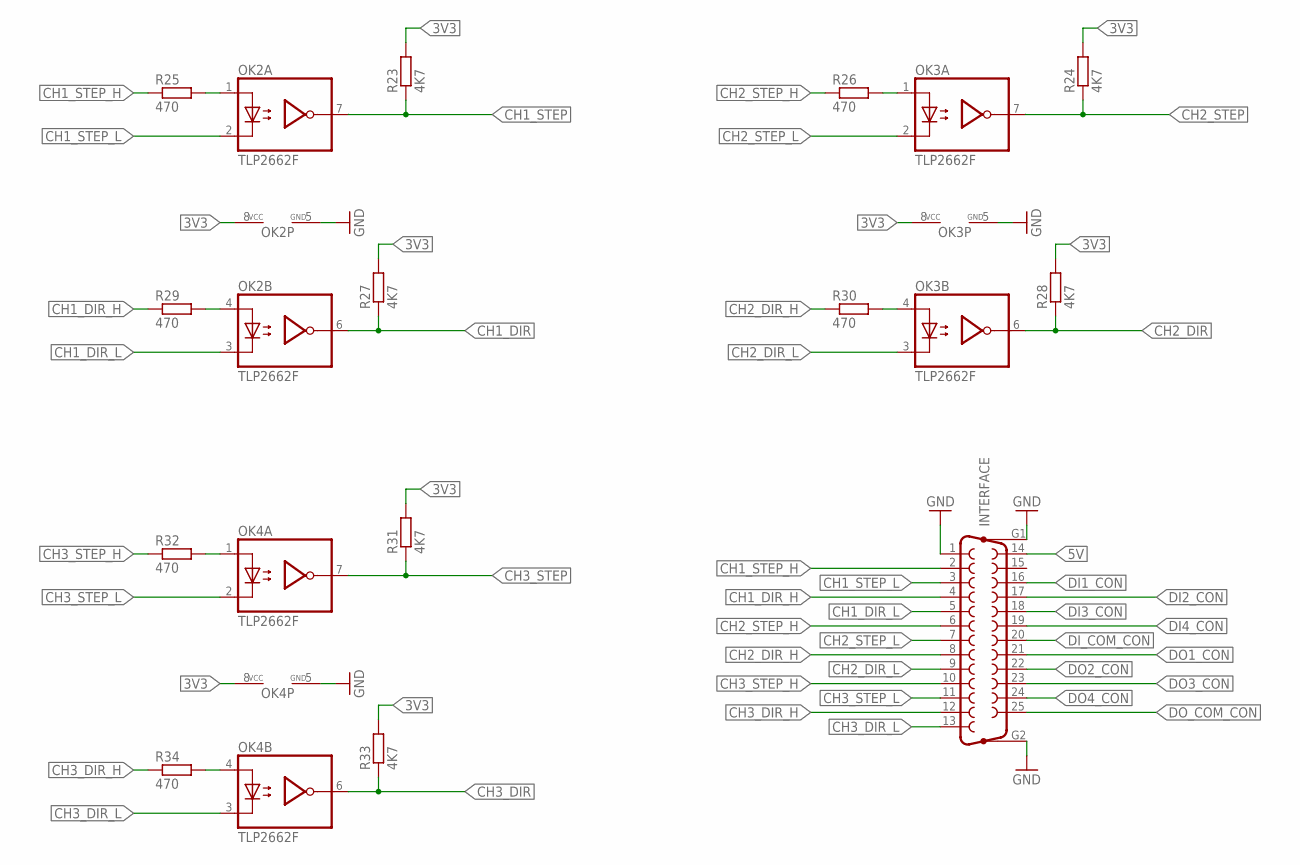
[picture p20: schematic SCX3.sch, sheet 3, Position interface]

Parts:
INTERFACE: F25VP
OK2, OK3, OK4: TLP2662F; DIL08
R23, R24, R27, R28, R31, R33: 4K7; R0805
R25, R26, R29, R30, R32, R34: 470; R0805

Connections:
3V3: OK2.8 (VCC), OK3.8 (VCC), OK4.8 (VCC), R23.2, R24.2, R27.2, R28.2, R31.2, R33.2; also elsewhere on the board
5V: INTERFACE.14; also elsewhere on the board
CH1_DIR: OK2.6 (VO), R27.1; also elsewhere on the board
CH1_DIR_H: INTERFACE.4, R29.1
CH1_DIR_L: INTERFACE.5, OK2.3 (C)
CH1_STEP: OK2.7 (VO), R23.1; also elsewhere on the board
CH1_STEP_H: INTERFACE.2, R25.1
CH1_STEP_L: INTERFACE.3, OK2.2 (C)
CH2_DIR: OK3.6 (VO), R28.1; also elsewhere on the board
CH2_DIR_H: INTERFACE.8, R30.1
CH2_DIR_L: INTERFACE.9, OK3.3 (C)
CH2_STEP: OK3.7 (VO), R24.1; also elsewhere on the board
CH2_STEP_H: INTERFACE.6, R26.1
CH2_STEP_L: INTERFACE.7, OK3.2 (C)
CH3_DIR: OK4.6 (VO), R33.1; also elsewhere on the board
CH3_DIR_H: INTERFACE.12, R34.1
CH3_DIR_L: INTERFACE.13, OK4.3 (C)
CH3_STEP: OK4.7 (VO), R31.1; also elsewhere on the board
CH3_STEP_H: INTERFACE.10, R32.1
CH3_STEP_L: INTERFACE.11, OK4.2 (C)
DI1_CON: INTERFACE.16; also elsewhere on the board
DI2_CON: INTERFACE.17; also elsewhere on the board
DI3_CON: INTERFACE.18; also elsewhere on the board
DI4_CON: INTERFACE.19; also elsewhere on the board
DI_COM_CON: INTERFACE.20; also elsewhere on the board
DO1_CON: INTERFACE.21; also elsewhere on the board
DO2_CON: INTERFACE.22; also elsewhere on the board
DO3_CON: INTERFACE.23; also elsewhere on the board
DO4_CON: INTERFACE.24; also elsewhere on the board
DO_COM_CON: INTERFACE.25; also elsewhere on the board
GND: INTERFACE.1, INTERFACE.G1, INTERFACE.G2, OK2.5 (GND), OK3.5 (GND), OK4.5 (GND); also elsewhere on the board
unnamed: OK3.4 (A), R30.2
unnamed: OK3.1 (A), R26.2
unnamed: OK4.4 (A), R34.2
unnamed: OK4.1 (A), R32.2
unnamed: OK2.4 (A), R29.2
unnamed: OK2.1 (A), R25.2

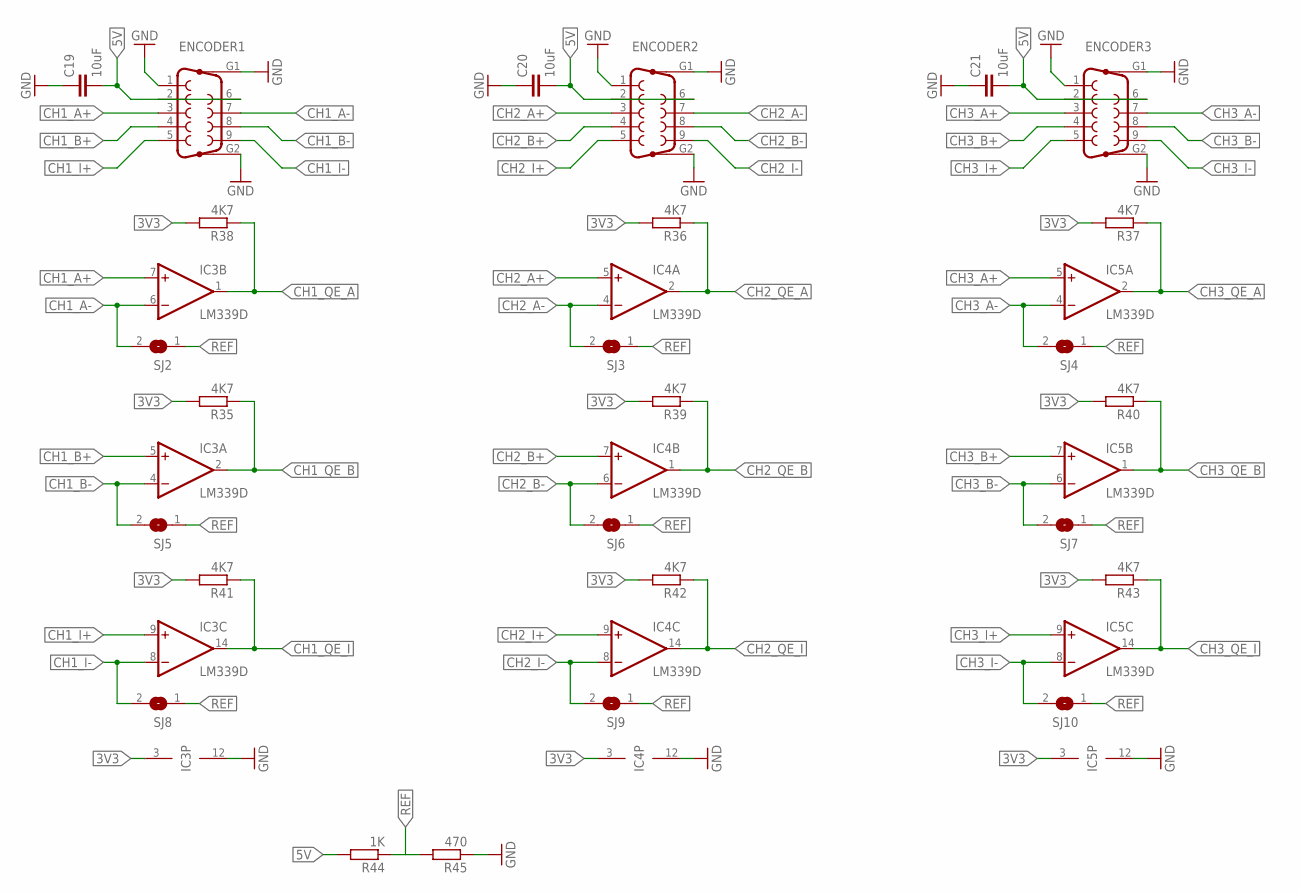
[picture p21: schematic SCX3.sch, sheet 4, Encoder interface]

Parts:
C19, C20, C21: 10uF; C0805
ENCODER1, ENCODER2, ENCODER3: F09VP
IC3, IC4, IC5: LM339D; SO14
R35, R36, R37, R38, R39, R40, R41, R42, R43: 4K7; R0805
R44: 1K; R0805
R45: 470; R0805
SJ2, SJ3, SJ4, SJ5, SJ6, SJ7, SJ8, SJ9, SJ10: SJ

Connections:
3V3: IC3.3 (V+), IC4.3 (V+), IC5.3 (V+), R35.2, R36.2, R37.2, R38.2, R39.2, R40.2, R41.2, R42.2, R43.2; also elsewhere on the board
5V: C19.2, C20.2, C21.2, ENCODER1.2, ENCODER1.6, ENCODER2.2, ENCODER2.6, ENCODER3.2, ENCODER3.6, R44.2; also elsewhere on the board
CH1_A+: ENCODER1.3, IC3.7 (+IN)
CH1_A-: ENCODER1.7, IC3.6 (-IN), SJ2.2
CH1_B+: ENCODER1.4, IC3.5 (+IN)
CH1_B-: ENCODER1.8, IC3.4 (-IN), SJ5.2
CH1_I+: ENCODER1.5, IC3.9 (+IN)
CH1_I-: ENCODER1.9, IC3.8 (-IN), SJ8.2
CH1_QE_A: IC3.1 (OUT), R38.1; also elsewhere on the board
CH1_QE_B: IC3.2 (OUT), R35.1; also elsewhere on the board
CH1_QE_I: IC3.14 (OUT), R41.1; also elsewhere on the board
CH2_A+: ENCODER2.3, IC4.5 (+IN)
CH2_A-: ENCODER2.7, IC4.4 (-IN), SJ3.2
CH2_B+: ENCODER2.4, IC4.7 (+IN)
CH2_B-: ENCODER2.8, IC4.6 (-IN), SJ6.2
CH2_I+: ENCODER2.5, IC4.9 (+IN)
CH2_I-: ENCODER2.9, IC4.8 (-IN), SJ9.2
CH2_QE_A: IC4.2 (OUT), R36.1; also elsewhere on the board
CH2_QE_B: IC4.1 (OUT), R39.1; also elsewhere on the board
CH2_QE_I: IC4.14 (OUT), R42.1; also elsewhere on the board
CH3_A+: ENCODER3.3, IC5.5 (+IN)
CH3_A-: ENCODER3.7, IC5.4 (-IN), SJ4.2
CH3_B+: ENCODER3.4, IC5.7 (+IN)
CH3_B-: ENCODER3.8, IC5.6 (-IN), SJ7.2
CH3_I+: ENCODER3.5, IC5.9 (+IN)
CH3_I-: ENCODER3.9, IC5.8 (-IN), SJ10.2
CH3_QE_A: IC5.2 (OUT), R37.1; also elsewhere on the board
CH3_QE_B: IC5.1 (OUT), R40.1; also elsewhere on the board
CH3_QE_I: IC5.14 (OUT), R43.1; also elsewhere on the board
GND: C19.1, C20.1, C21.1, ENCODER1.1, ENCODER1.G1, ENCODER1.G2, ENCODER2.1, ENCODER2.G1, ENCODER2.G2, ENCODER3.1, ENCODER3.G1, ENCODER3.G2, IC3.12 (GND), IC4.12 (GND), IC5.12 (GND), R45.1; also elsewhere on the board
REF: R44.1, R45.2, SJ2.1, SJ3.1, SJ4.1, SJ5.1, SJ6.1, SJ7.1, SJ8.1, SJ9.1, SJ10.1

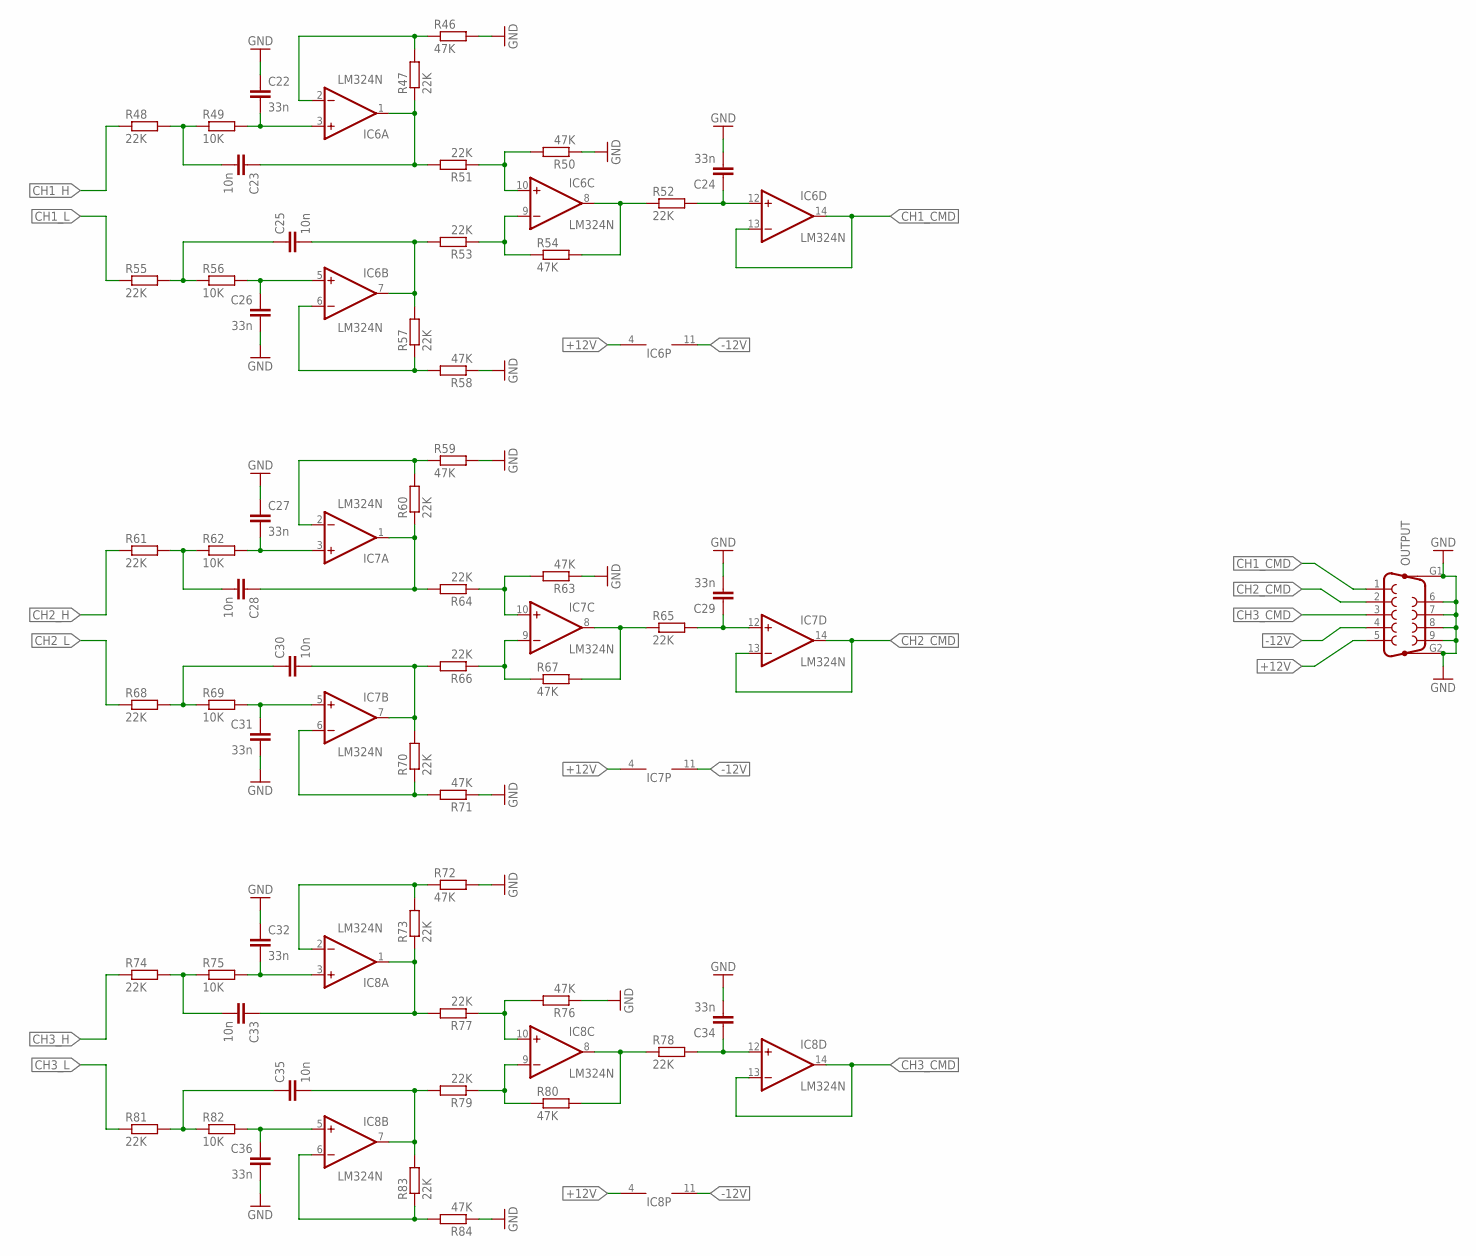
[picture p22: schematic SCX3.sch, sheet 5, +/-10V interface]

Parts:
C22, C24, C26, C27, C29, C31, C32, C34, C36: 33n; C0805
C23, C25, C28, C30, C33, C35: 10n; C0805
IC6, IC7, IC8: LM324N; DIL14
OUTPUT: F09VP
R46, R50, R54, R58, R59, R63, R67, R71, R72, R76, R80, R84: 47K; R0805
R47, R48, R51, R52, R53, R55, R57, R60, R61, R64, R65, R66, R68, R70, R73, R74, R77, R78, R79, R81, R83: 22K; R0805
R49, R56, R62, R69, R75, R82: 10K; R0805

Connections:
+12V: IC6.4 (V+), IC7.4 (V+), IC8.4 (V+), OUTPUT.5; also elsewhere on the board
-12V: IC6.11 (V-), IC7.11 (V-), IC8.11 (V-), OUTPUT.4; also elsewhere on the board
CH1_CMD: IC6.13 (-IN), IC6.14 (OUT), OUTPUT.1
CH1_H: R48.1; also elsewhere on the board
CH1_L: R55.1; also elsewhere on the board
CH2_CMD: IC7.13 (-IN), IC7.14 (OUT), OUTPUT.2
CH2_H: R61.1; also elsewhere on the board
CH2_L: R68.1; also elsewhere on the board
CH3_CMD: IC8.13 (-IN), IC8.14 (OUT), OUTPUT.3
CH3_H: R74.1; also elsewhere on the board
CH3_L: R81.1; also elsewhere on the board
GND: C22.1, C24.2, C26.2, C27.1, C29.2, C31.2, C32.1, C34.2, C36.2, OUTPUT.6, OUTPUT.7, OUTPUT.8, OUTPUT.9, OUTPUT.G1, OUTPUT.G2, R46.2, R50.1, R58.1, R59.2, R63.1, R71.1, R72.2, R76.1, R84.1; also elsewhere on the board
unnamed: IC6.6 (-IN), R57.1, R58.2
unnamed: IC6.2 (-IN), R46.1, R47.2
unnamed: C23.1, IC6.1 (OUT), R47.1, R51.2
unnamed: C22.2, IC6.3 (+IN), R49.2
unnamed: C23.2, R48.2, R49.1
unnamed: C24.1, IC6.12 (+IN), R52.2
unnamed: IC6.8 (OUT), R52.1, R54.2
unnamed: IC6.9 (-IN), R53.1, R54.1
unnamed: C25.2, IC6.7 (OUT), R53.2, R57.2
unnamed: C26.1, IC6.5 (+IN), R56.2
unnamed: C25.1, R55.2, R56.1
unnamed: IC6.10 (+IN), R50.2, R51.1
unnamed: IC7.6 (-IN), R70.1, R71.2
unnamed: IC7.2 (-IN), R59.1, R60.2
unnamed: C28.1, IC7.1 (OUT), R60.1, R64.2
unnamed: C27.2, IC7.3 (+IN), R62.2
unnamed: C28.2, R61.2, R62.1
unnamed: C29.1, IC7.12 (+IN), R65.2
unnamed: IC7.8 (OUT), R65.1, R67.2
unnamed: IC7.9 (-IN), R66.1, R67.1
unnamed: C30.2, IC7.7 (OUT), R66.2, R70.2
unnamed: C31.1, IC7.5 (+IN), R69.2
unnamed: C30.1, R68.2, R69.1
unnamed: IC7.10 (+IN), R63.2, R64.1
unnamed: IC8.6 (-IN), R83.1, R84.2
unnamed: IC8.2 (-IN), R72.1, R73.2
unnamed: C33.1, IC8.1 (OUT), R73.1, R77.2
unnamed: C32.2, IC8.3 (+IN), R75.2
unnamed: C33.2, R74.2, R75.1
unnamed: C34.1, IC8.12 (+IN), R78.2
unnamed: IC8.8 (OUT), R78.1, R80.2
unnamed: IC8.9 (-IN), R79.1, R80.1
unnamed: C35.2, IC8.7 (OUT), R79.2, R83.2
unnamed: C36.1, IC8.5 (+IN), R82.2
unnamed: C35.1, R81.2, R82.1
unnamed: IC8.10 (+IN), R76.2, R77.1

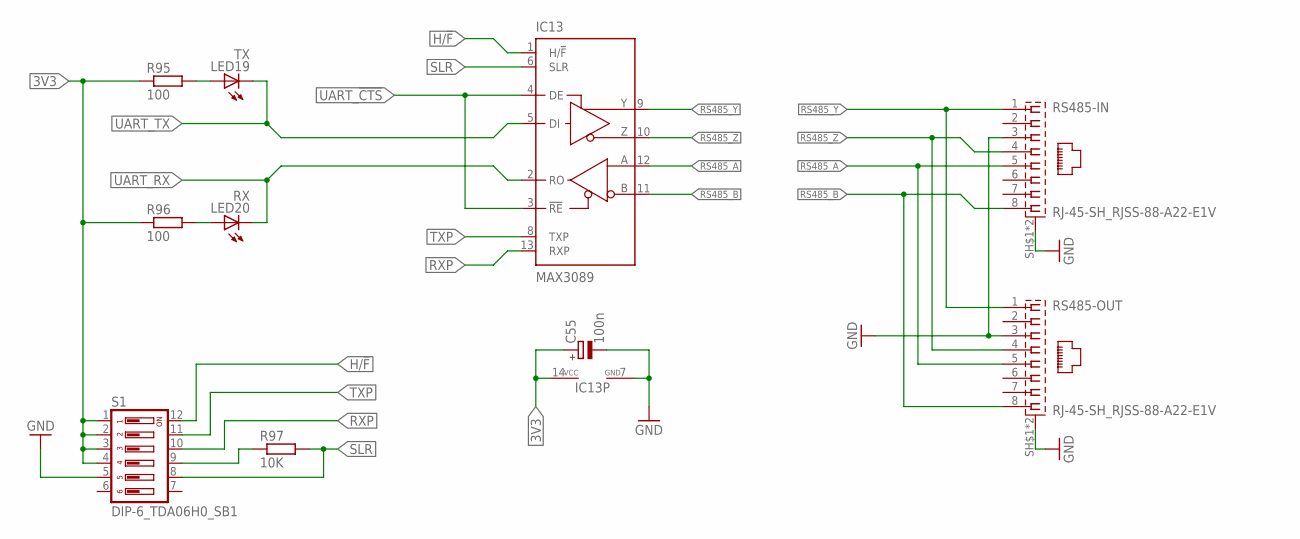
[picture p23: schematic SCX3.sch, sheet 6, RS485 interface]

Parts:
C55: 100n; UD-4X5,8_NICHICON
IC13: MAX3089; SO14
LED19: TX; SML0603
LED20: RX; SML0603
R95, R96: 100; R0603
R97: 10K; R0603
RS485-IN, RS485-OUT: RJ-45-SH_RJSS-88-A22-E1V; RJ-45M
S1: DIP-6_TDA06H0_SB1; TDA06H0_S

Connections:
3V3: C55.+, IC13.14 (VCC), R95.1, R96.1, S1.1, S1.2, S1.3, S1.4; also elsewhere on the board
GND: C55.-, IC13.7 (GND), RS485-IN.3, RS485-IN.SH$1 (SH), RS485-IN.SH$2 (SH), RS485-OUT.3, RS485-OUT.SH$1 (SH), RS485-OUT.SH$2 (SH), S1.5; also elsewhere on the board
H/!F: IC13.1 (H/!F), S1.12
unnamed: LED19.A, R95.2
unnamed: LED20.A, R96.2
unnamed: R97.1, S1.9
RS485_A: IC13.12 (A), RS485-IN.5, RS485-OUT.5
RS485_B: IC13.11 (B), RS485-IN.8, RS485-OUT.8
RS485_Y: IC13.9 (Y), RS485-IN.1, RS485-OUT.1
RS485_Z: IC13.10 (Z), RS485-IN.4, RS485-OUT.4
RXP: IC13.13 (RXP), S1.10
SLR: IC13.6 (SLR), R97.2, S1.8
TXP: IC13.8 (TXP), S1.11
UART_!CTS: IC13.3 (!RE), IC13.4 (DE); also elsewhere on the board
UART_RX: IC13.2 (RO), LED20.C; also elsewhere on the board
UART_TX: IC13.5 (DI), LED19.C; also elsewhere on the board

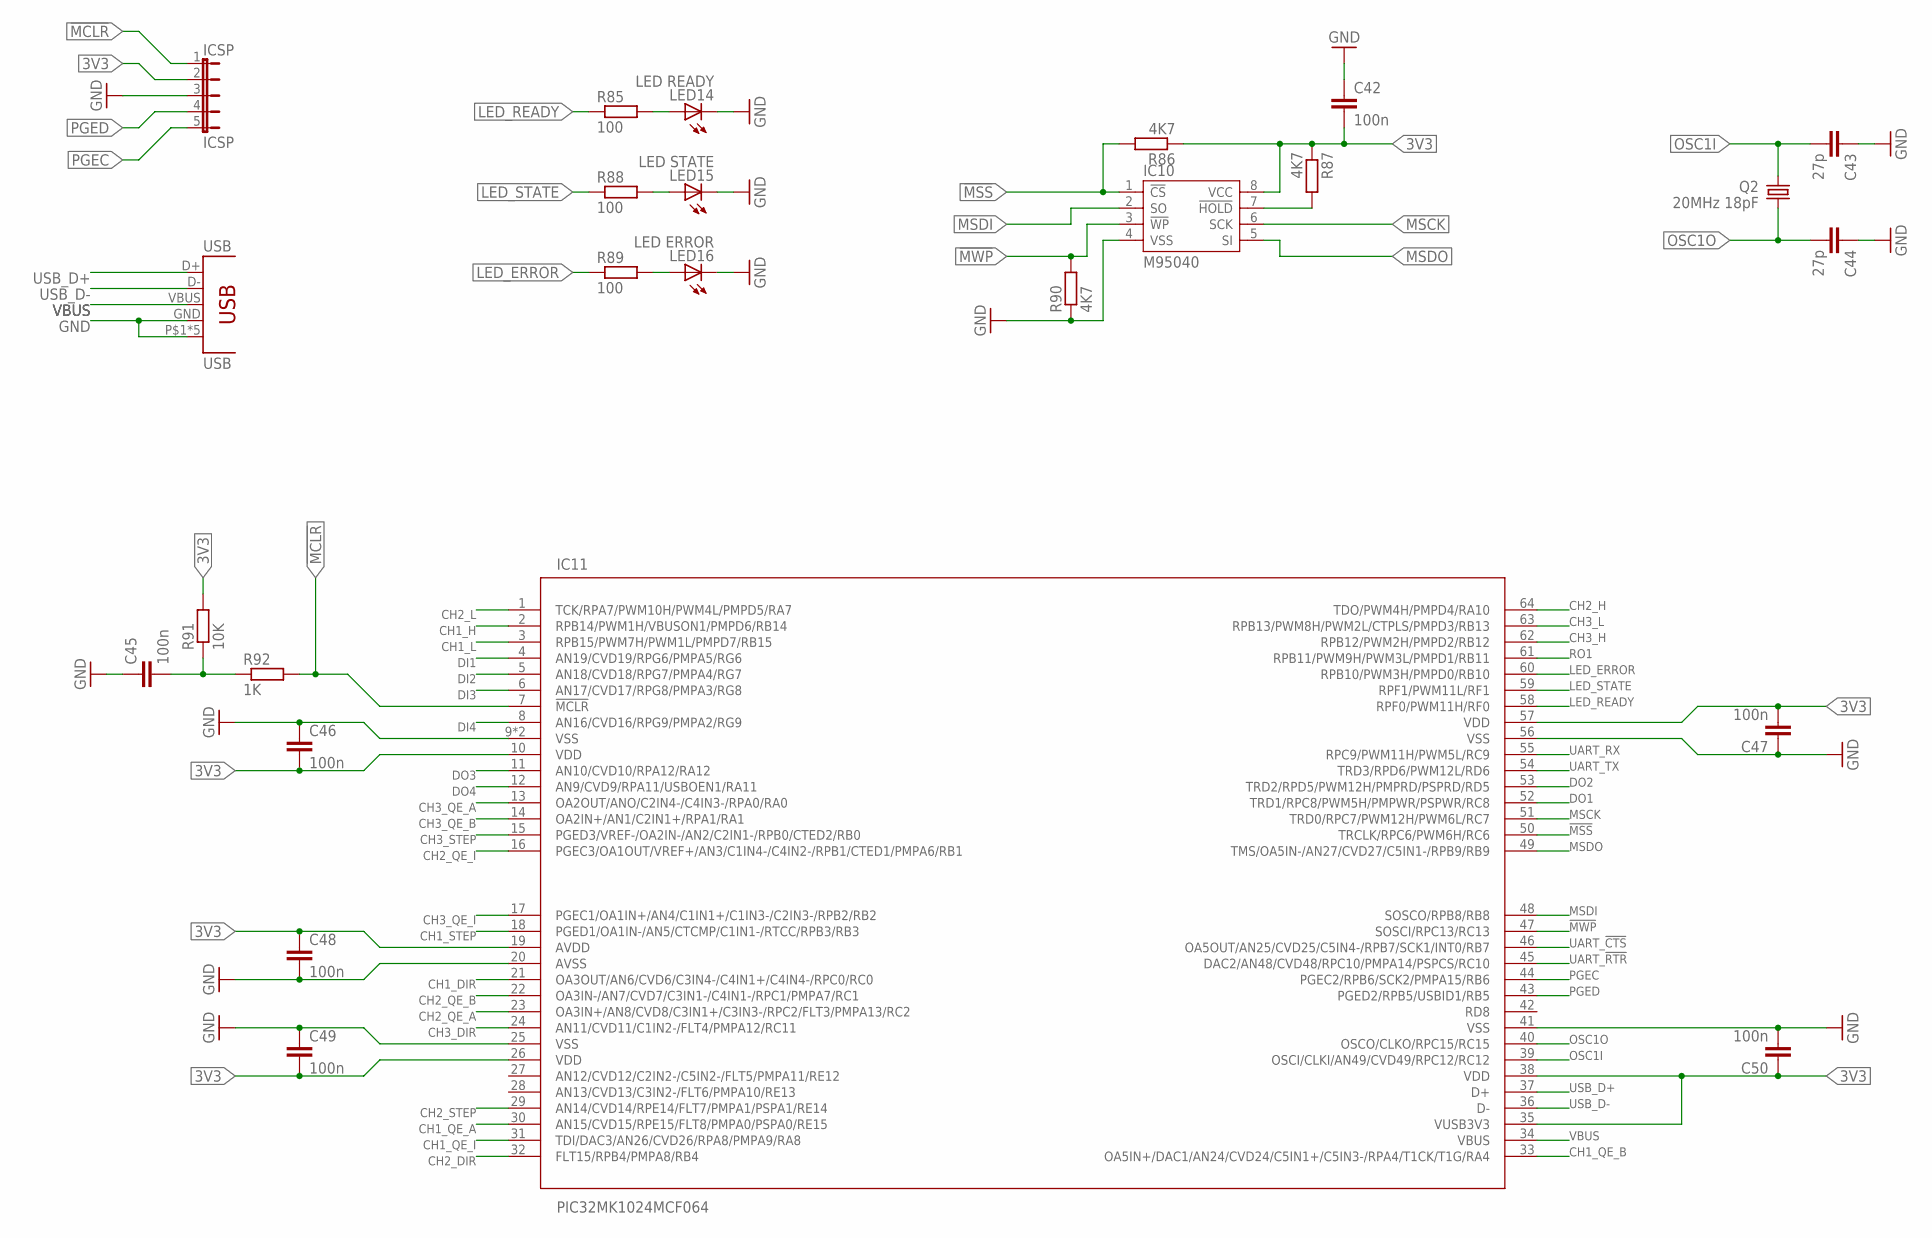
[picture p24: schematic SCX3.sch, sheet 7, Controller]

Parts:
C42, C45, C46, C47, C48, C49, C50: 100n; C0805
C43, C44: 27p; C0805
IC10: M95040; SO8
IC11: PIC32MK1024MCF064; QFN64-9X9
ICSP: ICSP; JP5
LED14: LED READY; SML1206
LED15: LED STATE; SML1206
LED16: LED ERROR; SML1206
Q2: 20MHz 18pF; SM49
R85, R88, R89: 100; R0805
R86, R87, R90: 4K7; R0805
R91: 10K; R0805
R92: 1K; R0805
USB: USB; USB-B-PTH-VERTICAL

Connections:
3V3: C42.2, C46.2, C47.2, C48.1, C49.2, C50.1, IC10.8 (VCC), IC11.10 (VDD), IC11.19 (AVDD), IC11.26 (VDD), IC11.35 (VUSB3V3), IC11.38 (VDD), IC11.57 (VDD), ICSP.2, R86.1, R87.1, R91.2; also elsewhere on the board
!HOLD: IC10.7 (!HOLD), R87.2
!MCLR: IC11.7 (!MCLR), ICSP.1, R92.2
!MSS: IC10.1 (!CS), IC11.50 (TRCLK/RPC6/PWM6H/RC6), R86.2
!MWP: IC10.3 (!WP), IC11.47 (SOSCI/RPC13/RC13), R90.2
CH1_DIR: IC11.21 (OA3OUT/AN6/CVD6/C3IN4-/C4IN1+/C4IN4-/RP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); also elsewhere on the board
CH1_H: IC11.2 (RPB14/PWM1H/VBUSON1/PMPD6/RB14); also elsewhere on the board
CH1_L: IC11.3 (RPB15/PWM7H/PWM1L/PMPD7/RB15); also elsewhere on the board
CH1_QE_A: IC11.30 (AN15/CVD15/RPE15/FLT8/PMPA0/PSPA0/RE15); also elsewhere on the board
CH1_QE_B: IC11.33 (OA5IN+/DAC1/AN24/CVD24/C5IN1+/C5IN3-/RP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); also elsewhere on the board
CH1_QE_I: IC11.31 (TDI/DAC3/AN26/CVD26/RPA8/PMPA9/RA8); also elsewhere on the board
CH1_STEP: IC11.18 (PGED1/OA1IN-/AN5/CTCMP/C1IN1-/RTCC/RPB3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); also elsewhere on the board
CH2_DIR: IC11.32 (FLT15/RPB4/PMPA8/RB4); also elsewhere on the board
CH2_H: IC11.64 (TDO/PWM4H/PMPD4/RA10); also elsewhere on the board
CH2_L: IC11.1 (TCK/RPA7/PWM10H/PWM4L/PMPD5/RA7); also elsewhere on the board
CH2_QE_A: IC11.23 (OA3IN+/AN8/CVD8/C3IN1+/C3IN3-/RPC2/FLT3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); also elsewhere on the board
CH2_QE_B: IC11.22 (OA3IN-/AN7/CVD7/C3IN1-/C4IN1-/RPC1/PMPA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); also elsewhere on the board
CH2_QE_I: IC11.16 (PGEC3/OA1OUT/VREF+/AN3/C1IN4-/C4IN2-/RP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); also elsewhere on the board
CH2_STEP: IC11.29 (AN14/CVD14/RPE14/FLT7/PMPA1/PSPA1/RE14); also elsewhere on the board
CH3_DIR: IC11.24 (AN11/CVD11/C1IN2-/FLT4/PMPA12/RC11); also elsewhere on the board
CH3_H: IC11.62 (RPB12/PWM2H/PMPD2/RB12); also elsewhere on the board
CH3_L: IC11.63 (RPB13/PWM8H/PWM2L/CTPLS/PMPD3/RB13); also elsewhere on the board
CH3_QE_A: IC11.13 (OA2OUT/ANO/C2IN4-/C4IN3-/RPA0/RA0); also elsewhere on the board
CH3_QE_B: IC11.14 (OA2IN+/AN1/C2IN1+/RPA1/RA1); also elsewhere on the board
CH3_QE_I: IC11.17 (PGEC1/OA1IN+/AN4/C1IN1+/C1IN3-/C2IN3-/R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); also elsewhere on the board
CH3_STEP: IC11.15 (PGED3/VREF-/OA2IN-/AN2/C2IN1-/RPB0/CTED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); also elsewhere on the board
DI1: IC11.4 (AN19/CVD19/RPG6/PMPA5/RG6); also elsewhere on the board
DI2: IC11.5 (AN18/CVD18/RPG7/PMPA4/RG7); also elsewhere on the board
DI3: IC11.6 (AN17/CVD17/RPG8/PMPA3/RG8); also elsewhere on the board
DI4: IC11.8 (AN16/CVD16/RPG9/PMPA2/RG9); also elsewhere on the board
DO1: IC11.52 (TRD1/RPC8/PWM5H/PMPWR/PSPWR/RC8); also elsewhere on the board
DO2: IC11.53 (TRD2/RPD5/PWM12H/PMPRD/PSPRD/RD5); also elsewhere on the board
DO3: IC11.11 (AN10/CVD10/RPA12/RA12); also elsewhere on the board
DO4: IC11.12 (AN9/CVD9/RPA11/USBOEN1/RA11); also elsewhere on the board
GND: C42.1, C43.1, C44.1, C45.1, C46.1, C47.1, C48.2, C49.1, C50.2, IC10.4 (VSS), IC11.9 (VSS), IC11.20 (AVSS), IC11.25 (VSS), IC11.41 (VSS), IC11.56 (VSS), IC11.EXP (VSS), ICSP.3, LED14.C, LED15.C, LED16.C, R90.1, USB.GND (4), USB.P$1 (5), USB.P$2 (5), USB.P$3 (5), USB.P$4 (5), USB.P$5 (5); also elsewhere on the board
LED_ERROR: IC11.60 (RPB10/PWM3H/PMPD0/RB10), R89.1
LED_READY: IC11.58 (RPF0/PWM11H/RF0), R85.1
LED_STATE: IC11.59 (RPF1/PWM11L/RF1), R88.1
MSCK: IC10.6 (SCK), IC11.51 (TRD0/RPC7/PWM12H/PWM6L/RC7)
MSDI: IC10.2 (SO), IC11.48 (SOSCO/RPB8/RB8)
MSDO: IC10.5 (SI), IC11.49 (TMS/OA5IN-/AN27/CVD27/C5IN1-/RPB9/RB9)
unnamed: LED14.A, R85.2
unnamed: LED15.A, R88.2
unnamed: LED16.A, R89.2
unnamed: C45.2, R91.1, R92.1
OSC1I: C43.2, IC11.39 (OSCI/CLKI/AN49/CVD49/RPC12/RC12), Q2.2
OSC1O: C44.2, IC11.40 (OSCO/CLKO/RPC15/RC15), Q2.1
PGEC: IC11.44 (PGEC2/RPB6/SCK2/PMPA15/RB6), ICSP.5
PGED: IC11.43 (PGED2/RPB5/USBID1/RB5), ICSP.4
RO1: IC11.61 (RPB11/PWM9H/PWM3L/PMPD1/RB11); also elsewhere on the board
UART_!CTS: IC11.46 (OA5OUT/AN25/CVD25/C5IN4-/RPB7/SCK1/INT0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); also elsewhere on the board
UART_!RTR: IC11.45 (DAC2/AN48/CVD48/RPC10/PMPA14/PSPCS/RC10)
UART_RX: IC11.55 (RPC9/PWM11H/PWM5L/RC9); also elsewhere on the board
UART_TX: IC11.54 (TRD3/RPD6/PWM12L/RD6); also elsewhere on the board
USB_D+: IC11.37 (D+), USB.D+ (1)
USB_D-: IC11.36 (D-), USB.D- (2)
VBUS: IC11.34 (VBUS), USB.VBUS (3)

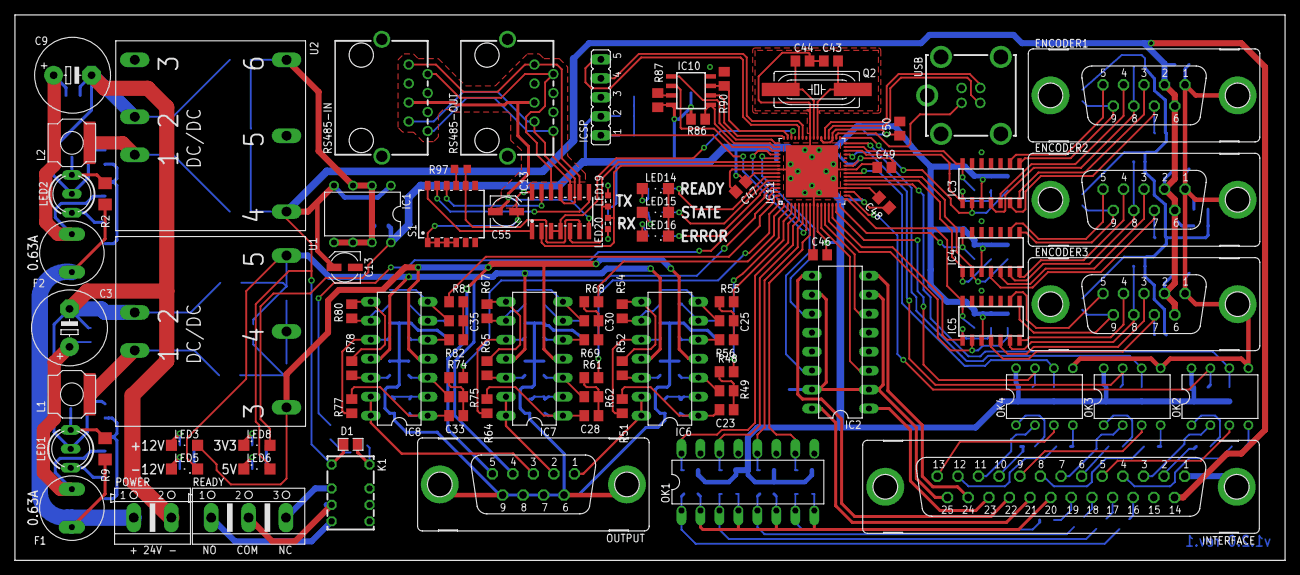
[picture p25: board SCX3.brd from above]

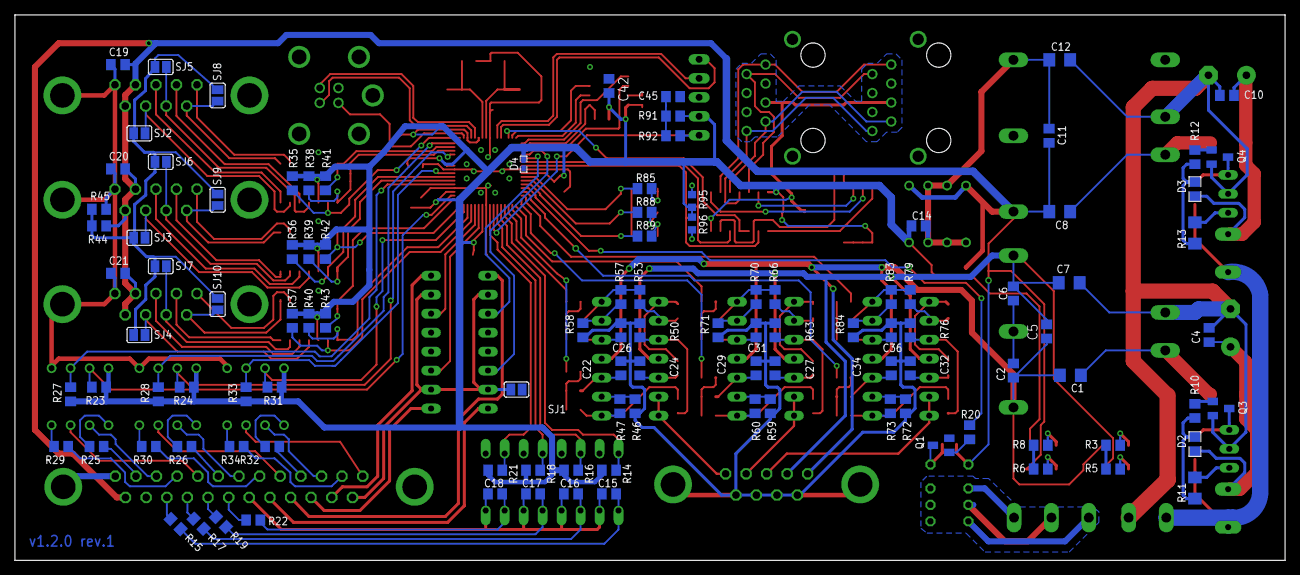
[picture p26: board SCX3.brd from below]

Board: 2 copper layers, 170.0 x 73.0 mm, 201 parts (110 on the bottom side), 183 nets.

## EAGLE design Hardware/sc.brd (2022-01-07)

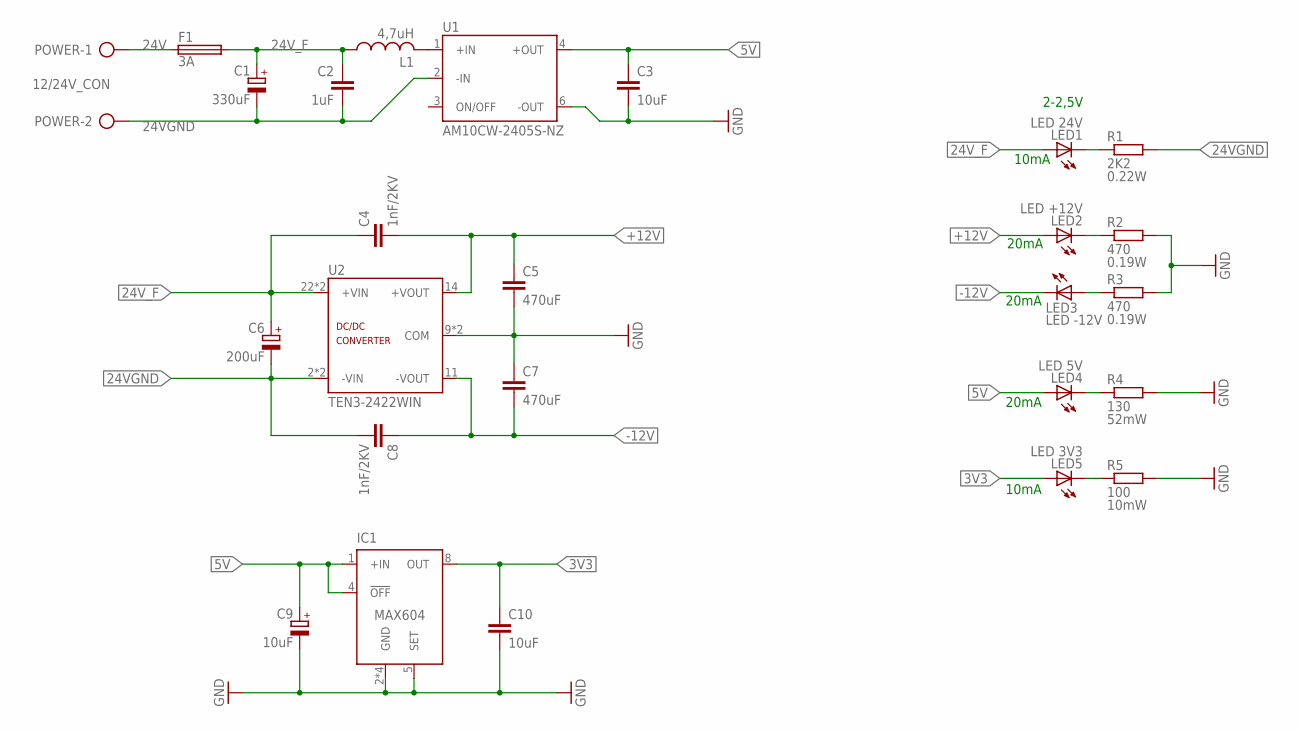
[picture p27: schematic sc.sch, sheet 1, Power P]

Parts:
C1: 330uF; E5-10,5
C2: 1uF; C0805
C3, C10: 10uF; C0805
C4, C8: 1nF/2KV; C0805
C5, C7: 470uF; C0805
C6: 200uF; E5-10,5
C9: 10uF; UD-4X5,8_NICHICON
F1: 3A; SH22,5
IC1: MAX604; DIL08
L1: 4,7uH; DJNR6028
LED1: LED 24V; SML1206
LED2: LED +12V; SML1206
LED3: LED -12V; SML1206
LED4: LED 5V; SML1206
LED5: LED 3V3; SML1206
POWER: 12/24V_CON; AK500/2
R1: 2K2; R1206
R2, R3: 470; R0805
R4: 130; R0805
R5: 100; R0805
U1: AM10CW-2405S-NZ; AM10CW-NZ
U2: TEN3-2422WIN; TEN3-WIN

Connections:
3V3: C10.1, IC1.8 (OUT), LED5.A; also elsewhere on the board
5V: C3.1, C9.+, IC1.1 (+IN), IC1.4 (!OFF), LED4.A, U1.4 (+OUT); also elsewhere on the board
24V: F1.1, POWER.1
24VGND: C1.-, C2.2, C6.-, C8.2, POWER.2, R1.2, U1.2 (-IN), U2.2 (-VIN), U2.3 (-VIN)
24V_F: C1.+, C2.1, C4.1, C6.+, F1.2, L1.A (1), LED1.A, U2.22 (+VIN), U2.23 (+VIN); also elsewhere on the board
+12V: C4.2, C5.1, LED2.A, U2.14 (+VOUT); also elsewhere on the board
-12V: C7.2, C8.1, LED3.C, U2.11 (-VOUT); also elsewhere on the board
GND: C3.2, C5.2, C7.1, C9.-, C10.2, IC1.2 (GND), IC1.3 (GND), IC1.5 (SET), IC1.6 (GND), IC1.7 (GND), R2.2, R3.2, R4.2, R5.2, U1.6 (-OUT), U2.9 (COM), U2.16 (COM); also elsewhere on the board
unnamed: LED1.C, R1.1
unnamed: L1.B (2), U1.1 (+IN)
unnamed: LED2.C, R2.1
unnamed: LED4.C, R4.1
unnamed: LED5.C, R5.1
unnamed: LED3.A, R3.1

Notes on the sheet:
2-2,5V
10mA
20mA

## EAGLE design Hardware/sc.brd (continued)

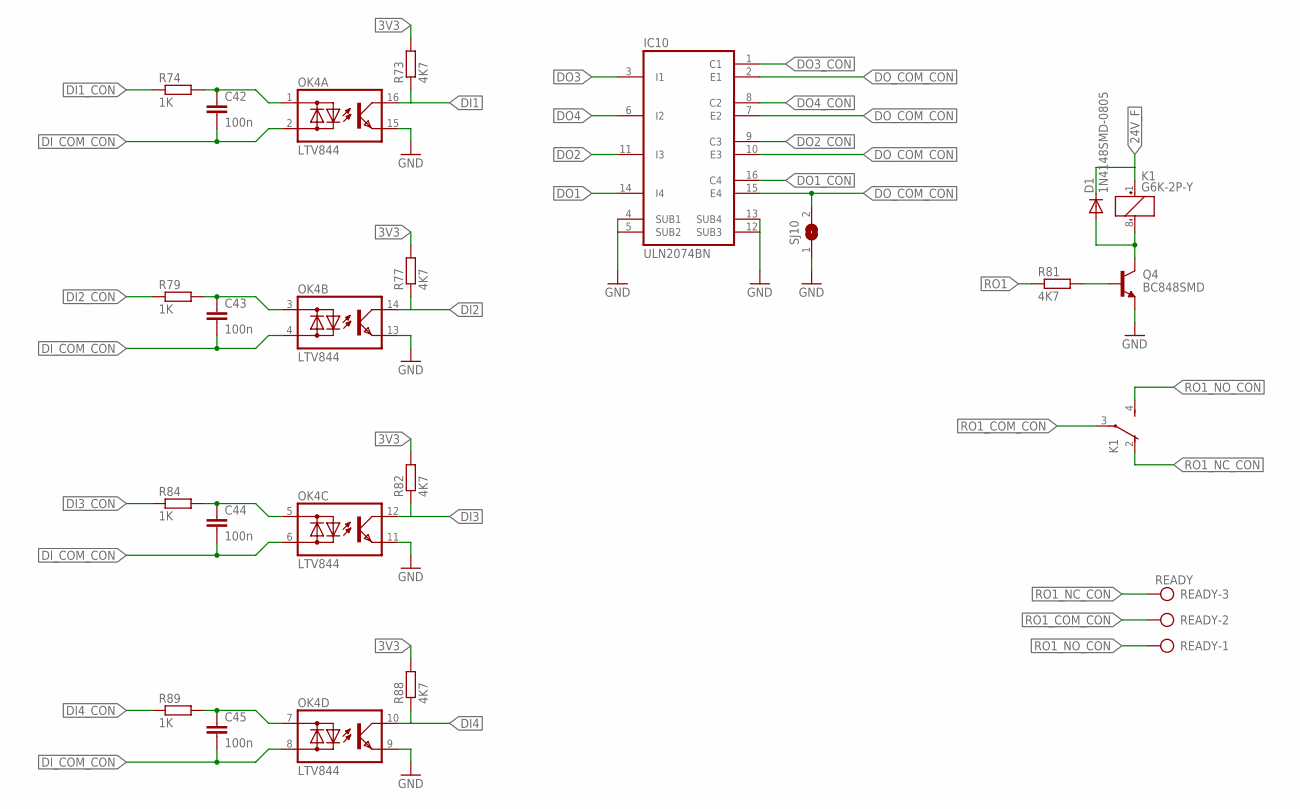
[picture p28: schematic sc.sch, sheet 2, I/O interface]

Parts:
C42, C43, C44, C45: 100n; C0805
D1: 1N4148SMD-0805; D0805
IC10: ULN2074BN; DIL16
K1: G6K-2P-Y
OK4: LTV844; DIL16
Q4: BC848SMD; SOT23
R73, R77, R81, R82, R88: 4K7; R0805
R74, R79, R84, R89: 1K; R0805
READY: READY; AK500/3
SJ10: SJ

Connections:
3V3: R73.2, R77.2, R82.2, R88.2; also elsewhere on the board
24V_F: D1.2 (C), K1.1 (+); also elsewhere on the board
DI1: OK4.16 (C), R73.1; also elsewhere on the board
DI1_CON: R74.1; also elsewhere on the board
DI2: OK4.14 (C), R77.1; also elsewhere on the board
DI2_CON: R79.1; also elsewhere on the board
DI3: OK4.12 (C), R82.1; also elsewhere on the board
DI3_CON: R84.1; also elsewhere on the board
DI4: OK4.10 (C), R88.1; also elsewhere on the board
DI4_CON: R89.1; also elsewhere on the board
DI_COM_CON: C42.2, C43.2, C44.2, C45.2, OK4.2 (AC2), OK4.4 (AC2), OK4.6 (AC2), OK4.8 (AC2); also elsewhere on the board
DO1: IC10.14 (I4); also elsewhere on the board
DO1H_CON: D1.1 (A), K1.8 (-), Q4.3 (C)
DO1_CON: IC10.16 (C4); also elsewhere on the board
DO2: IC10.11 (I3); also elsewhere on the board
DO2_CON: IC10.9 (C3); also elsewhere on the board
DO3: IC10.3 (I1); also elsewhere on the board
DO3_CON: IC10.1 (C1); also elsewhere on the board
DO4: IC10.6 (I2); also elsewhere on the board
DO4_CON: IC10.8 (C2); also elsewhere on the board
DO_COM_CON: IC10.2 (E1), IC10.7 (E2), IC10.10 (E3), IC10.15 (E4), SJ10.2; also elsewhere on the board
GND: IC10.4 (SUB1), IC10.5 (SUB2), IC10.12 (SUB3), IC10.13 (SUB4), OK4.9 (E), OK4.11 (E), OK4.13 (E), OK4.15 (E), Q4.2 (E), SJ10.1; also elsewhere on the board
unnamed: C43.1, OK4.3 (AC1), R79.2
unnamed: Q4.1 (B), R81.2
unnamed: C44.1, OK4.5 (AC1), R84.2
unnamed: C45.1, OK4.7 (AC1), R89.2
unnamed: C42.1, OK4.1 (AC1), R74.2
RO1: R81.1; also elsewhere on the board
RO1_COM_CON: K1.3, READY.2
RO1_NC_CON: K1.2 (O), READY.3
RO1_NO_CON: K1.4 (S), READY.1

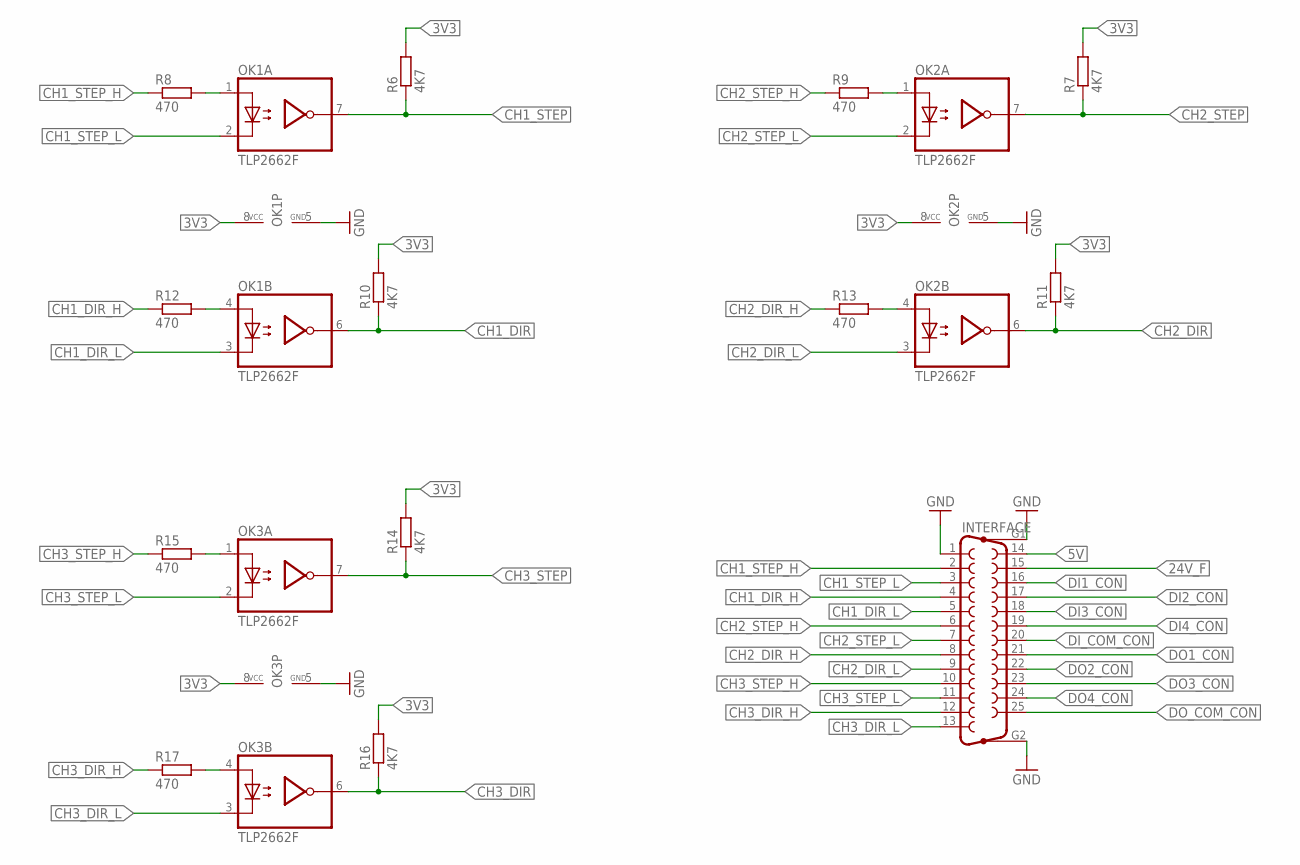
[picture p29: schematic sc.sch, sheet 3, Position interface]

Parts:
INTERFACE: F25VP
OK1, OK2, OK3: TLP2662F; DIL08
R6, R7, R10, R11, R14, R16: 4K7; R0805
R8, R9, R12, R13, R15, R17: 470; R0805

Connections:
3V3: OK1.8 (VCC), OK2.8 (VCC), OK3.8 (VCC), R6.2, R7.2, R10.2, R11.2, R14.2, R16.2; also elsewhere on the board
5V: INTERFACE.14; also elsewhere on the board
24V_F: INTERFACE.15; also elsewhere on the board
CH1_DIR: OK1.6 (VO), R10.1; also elsewhere on the board
CH1_DIR_H: INTERFACE.4, R12.1
CH1_DIR_L: INTERFACE.5, OK1.3 (C)
CH1_STEP: OK1.7 (VO), R6.1; also elsewhere on the board
CH1_STEP_H: INTERFACE.2, R8.1
CH1_STEP_L: INTERFACE.3, OK1.2 (C)
CH2_DIR: OK2.6 (VO), R11.1; also elsewhere on the board
CH2_DIR_H: INTERFACE.8, R13.1
CH2_DIR_L: INTERFACE.9, OK2.3 (C)
CH2_STEP: OK2.7 (VO), R7.1; also elsewhere on the board
CH2_STEP_H: INTERFACE.6, R9.1
CH2_STEP_L: INTERFACE.7, OK2.2 (C)
CH3_DIR: OK3.6 (VO), R16.1; also elsewhere on the board
CH3_DIR_H: INTERFACE.12, R17.1
CH3_DIR_L: INTERFACE.13, OK3.3 (C)
CH3_STEP: OK3.7 (VO), R14.1; also elsewhere on the board
CH3_STEP_H: INTERFACE.10, R15.1
CH3_STEP_L: INTERFACE.11, OK3.2 (C)
DI1_CON: INTERFACE.16; also elsewhere on the board
DI2_CON: INTERFACE.17; also elsewhere on the board
DI3_CON: INTERFACE.18; also elsewhere on the board
DI4_CON: INTERFACE.19; also elsewhere on the board
DI_COM_CON: INTERFACE.20; also elsewhere on the board
DO1_CON: INTERFACE.21; also elsewhere on the board
DO2_CON: INTERFACE.22; also elsewhere on the board
DO3_CON: INTERFACE.23; also elsewhere on the board
DO4_CON: INTERFACE.24; also elsewhere on the board
DO_COM_CON: INTERFACE.25; also elsewhere on the board
GND: INTERFACE.1, INTERFACE.G1, INTERFACE.G2, OK1.5 (GND), OK2.5 (GND), OK3.5 (GND); also elsewhere on the board
unnamed: OK2.4 (A), R13.2
unnamed: OK2.1 (A), R9.2
unnamed: OK3.4 (A), R17.2
unnamed: OK3.1 (A), R15.2
unnamed: OK1.4 (A), R12.2
unnamed: OK1.1 (A), R8.2


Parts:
C11, C12, C13: 10uF; C0805
ENCODER1, ENCODER2, ENCODER3: F09VP
IC2, IC3, IC4: LM339D; SO14
R18, R19, R20, R21, R22, R23, R24, R25, R26: 4K7; R0805
R27: 330; R0805
R28: 1K; R0805
SJ1, SJ2, SJ3, SJ4, SJ5, SJ6, SJ7, SJ8, SJ9: SJ

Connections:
2V5: R27.1, R28.2, SJ1.1, SJ2.1, SJ3.1, SJ4.1, SJ5.1, SJ6.1, SJ7.1, SJ8.1, SJ9.1
3V3: IC2.3 (V+), IC3.3 (V+), IC4.3 (V+), R18.2, R19.2, R20.2, R21.2, R22.2, R23.2, R24.2, R25.2, R26.2; also elsewhere on the board
5V: C11.2, C12.2, C13.2, ENCODER1.2, ENCODER1.6, ENCODER2.2, ENCODER2.6, ENCODER3.2, ENCODER3.6, R27.2; also elsewhere on the board
CH1_A+: ENCODER1.3, IC2.5 (+IN)
CH1_A-: ENCODER1.7, IC2.4 (-IN), SJ1.2
CH1_B+: ENCODER1.4, IC2.7 (+IN)
CH1_B-: ENCODER1.8, IC2.6 (-IN), SJ4.2
CH1_I+: ENCODER1.5, IC2.9 (+IN)
CH1_I-: ENCODER1.9, IC2.8 (-IN), SJ7.2
CH1_QE_A: IC2.2 (OUT), R18.1; also elsewhere on the board
CH1_QE_B: IC2.1 (OUT), R21.1; also elsewhere on the board
CH1_QE_I: IC2.14 (OUT), R24.1; also elsewhere on the board
CH2_A+: ENCODER2.3, IC3.5 (+IN)
CH2_A-: ENCODER2.7, IC3.4 (-IN), SJ2.2
CH2_B+: ENCODER2.4, IC3.7 (+IN)
CH2_B-: ENCODER2.8, IC3.6 (-IN), SJ5.2
CH2_I+: ENCODER2.5, IC3.9 (+IN)
CH2_I-: ENCODER2.9, IC3.8 (-IN), SJ8.2
CH2_QE_A: IC3.2 (OUT), R19.1; also elsewhere on the board
CH2_QE_B: IC3.1 (OUT), R22.1; also elsewhere on the board
CH2_QE_I: IC3.14 (OUT), R25.1; also elsewhere on the board
CH3_A+: ENCODER3.3, IC4.5 (+IN)
CH3_A-: ENCODER3.7, IC4.4 (-IN), SJ3.2
CH3_B+: ENCODER3.4, IC4.7 (+IN)
CH3_B-: ENCODER3.8, IC4.6 (-IN), SJ6.2
CH3_I+: ENCODER3.5, IC4.9 (+IN)
CH3_I-: ENCODER3.9, IC4.8 (-IN), SJ9.2
CH3_QE_A: IC4.2 (OUT), R20.1; also elsewhere on the board
CH3_QE_B: IC4.1 (OUT), R23.1; also elsewhere on the board
CH3_QE_I: IC4.14 (OUT), R26.1; also elsewhere on the board
GND: C11.1, C12.1, C13.1, ENCODER1.1, ENCODER1.G1, ENCODER1.G2, ENCODER2.1, ENCODER2.G1, ENCODER2.G2, ENCODER3.1, ENCODER3.G1, ENCODER3.G2, IC2.12 (GND), IC3.12 (GND), IC4.12 (GND), R28.1; also elsewhere on the board


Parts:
C14, C16, C18, C19, C21, C23, C24, C26, C28: 33n; C0805
C15, C17, C20, C22, C25, C27: 10n; C0805
IC5, IC6, IC7: LM324N; DIL14
OUTPUT: F09VP
R29, R33, R37, R41, R42, R46, R50, R54, R55, R59, R63, R67: 47K; R0805
R30, R31, R34, R35, R36, R38, R40, R43, R44, R47, R48, R49, R51, R53, R56, R57, R60, R61, R62, R64, R66: 22K; R0805
R32, R39, R45, R52, R58, R65: 10K; R0805

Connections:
+12V: IC5.4 (V+), IC6.4 (V+), IC7.4 (V+); also elsewhere on the board
-12V: IC5.11 (V-), IC6.11 (V-), IC7.11 (V-); also elsewhere on the board
CH1_CMD: IC5.13 (-IN), IC5.14 (OUT), OUTPUT.1
CH1_H: R31.1; also elsewhere on the board
CH1_L: R38.1; also elsewhere on the board
CH2_CMD: IC6.13 (-IN), IC6.14 (OUT), OUTPUT.2
CH2_H: R44.1; also elsewhere on the board
CH2_L: R51.1; also elsewhere on the board
CH3_CMD: IC7.13 (-IN), IC7.14 (OUT), OUTPUT.3
CH3_H: R57.1; also elsewhere on the board
CH3_L: R64.1; also elsewhere on the board
GND: C14.1, C16.2, C18.2, C19.1, C21.2, C23.2, C24.1, C26.2, C28.2, OUTPUT.6, OUTPUT.7, OUTPUT.8, OUTPUT.9, OUTPUT.G1, OUTPUT.G2, R29.2, R33.1, R41.1, R42.2, R46.1, R54.1, R55.2, R59.1, R67.1; also elsewhere on the board
unnamed: IC5.6 (-IN), R40.1, R41.2
unnamed: IC5.2 (-IN), R29.1, R30.2
unnamed: C15.1, IC5.1 (OUT), R30.1, R34.2
unnamed: C14.2, IC5.3 (+IN), R32.2
unnamed: C15.2, R31.2, R32.1
unnamed: C16.1, IC5.12 (+IN), R35.2
unnamed: IC5.8 (OUT), R35.1, R37.2
unnamed: IC5.9 (-IN), R36.1, R37.1
unnamed: C17.2, IC5.7 (OUT), R36.2, R40.2
unnamed: C18.1, IC5.5 (+IN), R39.2
unnamed: C17.1, R38.2, R39.1
unnamed: IC5.10 (+IN), R33.2, R34.1
unnamed: IC6.6 (-IN), R53.1, R54.2
unnamed: IC6.2 (-IN), R42.1, R43.2
unnamed: C20.1, IC6.1 (OUT), R43.1, R47.2
unnamed: C19.2, IC6.3 (+IN), R45.2
unnamed: C20.2, R44.2, R45.1
unnamed: C21.1, IC6.12 (+IN), R48.2
unnamed: IC6.8 (OUT), R48.1, R50.2
unnamed: IC6.9 (-IN), R49.1, R50.1
unnamed: C22.2, IC6.7 (OUT), R49.2, R53.2
unnamed: C23.1, IC6.5 (+IN), R52.2
unnamed: C22.1, R51.2, R52.1
unnamed: IC6.10 (+IN), R46.2, R47.1
unnamed: IC7.6 (-IN), R66.1, R67.2
unnamed: IC7.2 (-IN), R55.1, R56.2
unnamed: C25.1, IC7.1 (OUT), R56.1, R60.2
unnamed: C24.2, IC7.3 (+IN), R58.2
unnamed: C25.2, R57.2, R58.1
unnamed: C26.1, IC7.12 (+IN), R61.2
unnamed: IC7.8 (OUT), R61.1, R63.2
unnamed: IC7.9 (-IN), R62.1, R63.1
unnamed: C27.2, IC7.7 (OUT), R62.2, R66.2
unnamed: C28.1, IC7.5 (+IN), R65.2
unnamed: C27.1, R64.2, R65.1
unnamed: IC7.10 (+IN), R59.2, R60.1


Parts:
C29, C30, C31, C32: 100n; C0805
C33: 100n; UD-4X5,8_NICHICON
IC8: MAX3221CAE; SSOP16
RS-232: F09VP

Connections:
3V3: C33.+, IC8.15 (VCC), IC8.16 (!FORCEOFF); also elsewhere on the board
GND: C31.2, C32.2, C33.-, IC8.1 (!EN), IC8.12 (FORCEON), IC8.14 (GND), RS-232.5, RS-232.G1, RS-232.G2; also elsewhere on the board
unnamed: C30.2, IC8.4 (C1-)
unnamed: C30.1, IC8.2 (C1+)
unnamed: C29.2, IC8.6 (C2-)
unnamed: C29.1, IC8.5 (C2+)
unnamed: C31.1, IC8.3 (V+)
unnamed: C32.1, IC8.7 (V-)
RS232_RX: IC8.8 (R1IN), RS-232.2
RS232_TX: IC8.13 (T1OUT), RS-232.3
UART_RX: IC8.9 (R1OUT); also elsewhere on the board
UART_TX: IC8.11 (T1IN); also elsewhere on the board


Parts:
C34, C35, C36, C37, C39, C40: 100n; C0805
C38, C41: 27p; C0805
IC9: PIC32; QFN64-9X9
ICSP: ICSP; JP5
LED6: LED READY; SML1206
LED7: LED STATE; SML1206
LED8: LED ERROR; SML1206
Q1: 20MHz 18pF; SM49
R68, R69, R70: 100; R0805
R71: 10K; R0805
R72: 1K; R0805

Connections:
3V3: C35.2, C36.2, C37.1, C39.2, C40.1, IC9.10 (VDD), IC9.19 (AVDD), IC9.26 (VDD), IC9.35 (VUSB3V3), IC9.38 (VDD), IC9.57 (VDD), ICSP.2, R71.2; also elsewhere on the board
!MCLR: IC9.7 (!MCLR), ICSP.1, R72.2
CH1_DIR: IC9.21 (OA3OUT/AN6/CVD6/C3IN4-/C4IN1+/C4IN4-/RP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); also elsewhere on the board
CH1_H: IC9.2 (RPB14/PWM1H/VBUSON1/PMPD6/RB14); also elsewhere on the board
CH1_L: IC9.3 (RPB15/PWM7H/PWM1L/PMPD7/RB15); also elsewhere on the board
CH1_QE_A: IC9.31 (TDI/DAC3/AN26/CVD26/RPA8/PMPA9/RA8); also elsewhere on the board
CH1_QE_B: IC9.30 (AN15/CVD15/RPE15/FLT8/PMPA0/PSPA0/RE15); also elsewhere on the board
CH1_QE_I: IC9.33 (OA5IN+/DAC1/AN24/CVD24/C5IN1+/C5IN3-/RP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); also elsewhere on the board
CH1_STEP: IC9.18 (PGED1/OA1IN-/AN5/CTCMP/C1IN1-/RTCC/RPB3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); also elsewhere on the board
CH2_DIR: IC9.32 (FLT15/RPB4/PMPA8/RB4); also elsewhere on the board
CH2_H: IC9.64 (TDO/PWM4H/PMPD4/RA10); also elsewhere on the board
CH2_L: IC9.1 (TCK/RPA7/PWM10H/PWM4L/PMPD5/RA7); also elsewhere on the board
CH2_QE_A: IC9.23 (OA3IN+/AN8/CVD8/C3IN1+/C3IN3-/RPC2/FLT3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); also elsewhere on the board
CH2_QE_B: IC9.22 (OA3IN-/AN7/CVD7/C3IN1-/C4IN1-/RPC1/PMPA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); also elsewhere on the board
CH2_QE_I: IC9.16 (PGEC3/OA1OUT/VREF+/AN3/C1IN4-/C4IN2-/RP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); also elsewhere on the board
CH2_STEP: IC9.29 (AN14/CVD14/RPE14/FLT7/PMPA1/PSPA1/RE14); also elsewhere on the board
CH3_DIR: IC9.24 (AN11/CVD11/C1IN2-/FLT4/PMPA12/RC11); also elsewhere on the board
CH3_H: IC9.62 (RPB12/PWM2H/PMPD2/RB12); also elsewhere on the board
CH3_L: IC9.63 (RPB13/PWM8H/PWM2L/CTPLS/PMPD3/RB13); also elsewhere on the board
CH3_QE_A: IC9.13 (OA2OUT/ANO/C2IN4-/C4IN3-/RPA0/RA0); also elsewhere on the board
CH3_QE_B: IC9.14 (OA2IN+/AN1/C2IN1+/RPA1/RA1); also elsewhere on the board
CH3_QE_I: IC9.17 (PGEC1/OA1IN+/AN4/C1IN1+/C1IN3-/C2IN3-/R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); also elsewhere on the board
CH3_STEP: IC9.15 (PGED3/VREF-/OA2IN-/AN2/C2IN1-/RPB0/CTED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); also elsewhere on the board
DI1: IC9.4 (AN19/CVD19/RPG6/PMPA5/RG6); also elsewhere on the board
DI2: IC9.5 (AN18/CVD18/RPG7/PMPA4/RG7); also elsewhere on the board
DI3: IC9.6 (AN17/CVD17/RPG8/PMPA3/RG8); also elsewhere on the board
DI4: IC9.8 (AN16/CVD16/RPG9/PMPA2/RG9); also elsewhere on the board
DO1: IC9.52 (TRD1/RPC8/PWM5H/PMPWR/PSPWR/RC8); also elsewhere on the board
DO2: IC9.53 (TRD2/RPD5/PWM12H/PMPRD/PSPRD/RD5); also elsewhere on the board
DO3: IC9.11 (AN10/CVD10/RPA12/RA12); also elsewhere on the board
DO4: IC9.12 (AN9/CVD9/RPA11/USBOEN1/RA11); also elsewhere on the board
GND: C34.1, C35.1, C36.1, C37.2, C38.1, C39.1, C40.2, C41.1, IC9.9 (VSS), IC9.20 (AVSS), IC9.25 (VSS), IC9.41 (VSS), IC9.56 (VSS), IC9.EXP (VSS), ICSP.3, LED6.C, LED7.C, LED8.C; also elsewhere on the board
LED_ERROR: IC9.60 (RPB10/PWM3H/PMPD0/RB10), R70.1
LED_READY: IC9.58 (RPF0/PWM11H/RF0), R68.1
LED_STATE: IC9.59 (RPF1/PWM11L/RF1), R69.1
unnamed: LED6.A, R68.2
unnamed: LED7.A, R69.2
unnamed: LED8.A, R70.2
unnamed: C34.2, R71.1, R72.1
OSC1I: C38.2, IC9.39 (OSCI/CLKI/AN49/CVD49/RPC12/RC12), Q1.2
OSC1O: C41.2, IC9.40 (OSCO/CLKO/RPC15/RC15), Q1.1
PGEC: IC9.44 (PGEC2/RPB6/SCK2/PMPA15/RB6), ICSP.5
PGED: IC9.43 (PGED2/RPB5/USBID1/RB5), ICSP.4
RO1: IC9.61 (RPB11/PWM9H/PWM3L/PMPD1/RB11); also elsewhere on the board
UART_RX: IC9.55 (RPC9/PWM11H/PWM5L/RC9); also elsewhere on the board
UART_TX: IC9.54 (TRD3/RPD6/PWM12L/RD6); also elsewhere on the board

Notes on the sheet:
10-15mA
2-2,5V



Board: 2 copper layers, 157.0 x 72.0 mm, 175 parts (97 on the bottom side), 161 nets.

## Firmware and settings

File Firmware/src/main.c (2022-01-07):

/*
 * Servo Controller: 3 axis STEP/DIR to analog +/-10V interface
 * 2019 Mateusz Frydrych <thewituch@gmail.com>
 */

#include <xc.h>

/* ----------------------- System includes ----------------------------------*/
#include <stdlib.h>
#include <stdio.h>
#include <string.h>

#include "system.h
#include "memory.h

/* ----------------------- EEPROM includes ----------------------------------*/
#include "eeprom/eeprom.h

/* ----------------------- IO includes --------------------------------------*/
#include "io/io.h

/* ----------------------- PID includes -------------------------------------*/
#include "pid/pid.h

/* ----------------------- Modbus includes ----------------------------------*/
#include "modbus/include/mb.h
#include "modbus/include/mbport.h

/* ----------------------- Other includes -----------------------------------*/
#include "qei.h
#include "capture.h
#include "pwm.h
#include "crc/crc.h

/* ----------------------- Defines ------------------------------------------*/
typedef enum
{
    SYS_BOOT,
    SYS_NORMAL,
    SYS_SAFESTOP,
    SYS_ERROR
} eSYSMode;

// A safe operation makro to immediately go to SAFE_STOP program
#define SAFE_OP(result, operation) \
            if(result = operation) goto SAFE_STOP

/* ----------------------- Constant variables -------------------------------*/

/* ----------------------- Static variables ---------------------------------*/
static volatile eSYSMode eSystemMode;

static ePIDErrorCode ePIDStatus;
static eMBErrorCode eMBStatus;
static eEEPROMErrorCode eEEPROMStatus;

/* ----------------------- Function prototypes ------------------------------*/
int main(void);
void app(void);

/* ----------------------- Function implementations -------------------------*/
int
main(void)
{
    /* Init boot mode at system start */
    eSystemMode = SYS_BOOT;

    while (1)
    {
        /* Maintain state machines of all polled MPLAB Harmony modules. */
        app();
    }

    /* Execution should not come here during normal operation */
    return (EXIT_FAILURE);
}

void
app(void)
{
    switch (eSystemMode)
    {
        case SYS_BOOT:
        {
            /* Clear errors */
            ePIDStatus = PID_ENOERR;
            eMBStatus = MB_ENOERR;
            eEEPROMStatus = EEPROM_ENOERR;

            /* Disable system interrupts */
            disableInterrupts();

            /* Modbus
             * Init the Modbus peripherial, set slave id and enable protocol stack
             */
            SAFE_OP(eMBStatus, eMBInit(MB_RTU, 0x0A, 2, 115200,
                                       MB_PAR_EVEN, MB_STOPB_ONE));
            SAFE_OP(eMBStatus, eMBSetSlaveID(0x0A, TRUE,
                                             ucSlaveID, sizeofa(ucSlaveID)));
            SAFE_OP(eMBStatus, eMBEnable());

            /* LED
             * Set STATE and ERROR led and clear other
             */
            LED_READY = OFF;
            LED_STATE = ON;
            LED_ERROR = OFF;

            setup_SYSTEM();
            setup_QEI();
            start_QEI();
            setup_CAPTURE();
            start_CAPTURE();
            setup_PWM();
            start_PWM();


            /* IO
             * Setup IO system
             */
            eIOSetup();


            /* EEPROM
             * Setup eeprom memory and register EE cells
             */
            SAFE_OP(eEEPROMStatus, eEEPROMSetup(EEPROM_HARDWARE));

            // Register EEPROM cells
            SAFE_OP(eEEPROMStatus,
                    eEEPROMRegisterEECell(&EECELLS.EE_PID1Config,
                                          &MEMORY.xPID1.xConfig,
                                          sizeof (MEMORY.xPID1.xConfig)));
            SAFE_OP(eEEPROMStatus,
                    eEEPROMRegisterEECell(&EECELLS.EE_PID2Config,
                                          &MEMORY.xPID2.xConfig,
                                          sizeof (MEMORY.xPID2.xConfig)));
            SAFE_OP(eEEPROMStatus,
                    eEEPROMRegisterEECell(&EECELLS.EE_PID3Config,
                                          &MEMORY.xPID3.xConfig,
                                          sizeof (MEMORY.xPID3.xConfig)));


            /* PID
             * Setup PID channels and run timer
             */
            const PIDConfig_t xPIDCleanConfig = {
                                                 0.35, 0.015f, 0.01f, 0.005f, 0.005f,
                                                 1.0f, 0.0f, 100.0f,
                                                 10000.0f, 15.0f, 16.0f, 17.0f,
                                                 -14457
            };
            SAFE_OP(ePIDStatus, ePIDInit(&MEMORY.xPID1, xPIDCleanConfig));
            SAFE_OP(ePIDStatus, ePIDInit(&MEMORY.xPID2, xPIDCleanConfig));
            SAFE_OP(ePIDStatus, ePIDInit(&MEMORY.xPID3, xPIDCleanConfig));

            // Setup calculation timer
            SAFE_OP(ePIDStatus, xPIDPortTimerInit(1));
            vPIDPortTimerEnable();

            // Enable modules
            SAFE_OP(ePIDStatus, ePIDEnable(&MEMORY.xPID1));
            SAFE_OP(ePIDStatus, ePIDEnable(&MEMORY.xPID2));
            SAFE_OP(ePIDStatus, ePIDEnable(&MEMORY.xPID3));

            /* Enable system interrupts */
            enableInterrupts();

            /* End boot sequence, go to normal operation mode */
            eSystemMode = SYS_NORMAL;
        }

        case SYS_NORMAL:
        {
            /* System
             * Incerase system cycle counter
             */
            MEMORY.ulSystemCycle++;

            /* LED
             * Set STATE and ERROR led and clear other
             */
            LED_READY = ON;
            LED_STATE = OFF;
            LED_ERROR = OFF;

            /* IO
             * Read inputs on cycle start
             */
            eIOReadInputs();


            /* Memory
             * Copy values to memory struct
             */
            MEMORY.lENCODER1 = (int32_t) ENCODER_CH1;
            MEMORY.lENCODER2 = (int32_t) ((int32_t) ENCODER_CH2 / 40.0f); //TESTING VAL
            MEMORY.lENCODER3 = (int32_t) ENCODER_CH3;

            MEMORY.lPOS1 = (int32_t) POSITION_CH1;
            MEMORY.lPOS2 = (int32_t) POSITION_CH2;
            MEMORY.lPOS3 = (int32_t) POSITION_CH3;

            MEMORY.xPID1.lCommand = (int32_t) (MEMORY.lPOS1);
            MEMORY.xPID2.lCommand = (int32_t) (MEMORY.lPOS2);
            MEMORY.xPID3.lCommand = (int32_t) (MEMORY.lPOS3);

            MEMORY.xPID1.lFeedback = (float32_t) MEMORY.lENCODER1;
            MEMORY.xPID2.lFeedback = (float32_t) MEMORY.lENCODER2;
            MEMORY.xPID3.lFeedback = (float32_t) MEMORY.lENCODER3;


            /* PID
             * Process PIDs and write to outputs
             */
            SAFE_OP(ePIDStatus, ePIDProcess(&MEMORY.xPID1));
            SAFE_OP(ePIDStatus, ePIDProcess(&MEMORY.xPID2));
            SAFE_OP(ePIDStatus, ePIDProcess(&MEMORY.xPID3));

            ANALOG_OUTPUT1 = (float32_t) MEMORY.xPID2.fOutput; //TESTING VAL
            ANALOG_OUTPUT2 = (float32_t) MEMORY.xPID2.fOutput;
            ANALOG_OUTPUT3 = (float32_t) MEMORY.xPID3.fOutput;


            /* System
             * Parse requests
             */
            if (MEMORY.xSystemRequest.READ == 1)
            {
                eEEPROMReadEECell(&EECELLS.EE_PID1Config);

                peEEPROMDataBlockRead(EECELLS.EE_PID2Config.address,
                                      EECELLS.EE_PID2Config.object,
                                      EECELLS.EE_PID2Config.size);

                uint32_t tmp = 0;
                SAFE_OP(eEEPROMStatus, peEEPROMDataRead(128, &tmp));
                MEMORY.xSystemStatus.WORD = (uint16_t) tmp;

                MEMORY.xSystemRequest.READ = 0;
            }

            if (MEMORY.xSystemRequest.SAVE == 1)
            {
                uint16_t usCRC = ulCRCCalculate(CRC16_Modbus,
                                                &MEMORY.xPID1.xConfig,
                                                sizeof (MEMORY.xPID1.xConfig) -
                                                sizeof (MEMORY.xPID1.xConfig.ulCRC));
                MEMORY.xPID1.xConfig.ulCRC = (uint32_t) usCRC;
                eEEPROMSaveEECell(&EECELLS.EE_PID1Config);

                usCRC = ulCRCCalculate(CRC16_Modbus,
                                       &MEMORY.xPID2.xConfig,
                                       sizeof (MEMORY.xPID2.xConfig) -
                                       sizeof (MEMORY.xPID2.xConfig.ulCRC));
                MEMORY.xPID2.xConfig.ulCRC = (uint32_t) usCRC;
                peEEPROMDataBlockWrite(EECELLS.EE_PID2Config.address,
                                       EECELLS.EE_PID2Config.object,
                                       EECELLS.EE_PID2Config.size);

                uint32_t tmp = (uint32_t) MEMORY.xSystemStatus.WORD;
                SAFE_OP(eEEPROMStatus, peEEPROMDataWrite(128, tmp));

                MEMORY.xSystemRequest.SAVE = 0;
            }


            /* ModBUS
             * Poll protocol
             */
            eMBStatus = eMBPoll();


            /* System
             * Signal every 1000th cycle by STATE led toggle
             */
            if (MEMORY.ulSystemCycle % 1000 == 0)
            {
                LED_STATE = ~LED_STATE;
            }


            /* IO
             * Write outputs on cycle end
             */
            eIOWriteOutputs();

            break;
        }

SAFE_STOP:
        case SYS_SAFESTOP:
        {
            /* Safety
             * Perform a safe stop of all modules
             */

            /* LED
             * Set STATE and ERROR led and clear other
             */
            LED_READY = OFF;
            LED_STATE = ON;
            LED_ERROR = ON;

            // Reset outputs
            RELAY_OUTPUT1 = OFF;
            DIGITAL_OUTPUT1 = OFF;
            DIGITAL_OUTPUT2 = OFF;
            DIGITAL_OUTPUT3 = OFF;
            DIGITAL_OUTPUT4 = OFF;
            ANALOG_OUTPUT1 = 0.0f;
            ANALOG_OUTPUT2 = 0.0f;
            ANALOG_OUTPUT3 = 0.0f;
            eIOWriteOutputs();

            // Disable PID modules and timer
            ePIDDisable(&MEMORY.xPID1);
            ePIDDisable(&MEMORY.xPID2);
            ePIDDisable(&MEMORY.xPID3);
            vPIDPortTimerDisable();

            // Disable PWM
            stop_PWM();

            /* End safe stop sequence, go to system error mode */
            eSystemMode = SYS_ERROR;
        }

        case SYS_ERROR:
        {
            /* Lock in error */
            eSystemMode = SYS_ERROR;

            /* LED
             * Set ERROR led and clear other
             */
            LED_READY = OFF;
            LED_STATE = OFF;
            LED_ERROR = ON;

            eIOWriteOutputs();

            /* ModBUS
             * Poll protocol if error don't concern ModBUS module
             */
            if (eMBStatus == MB_ENOERR)
            {
                eMBStatus = eMBPoll();
            }

            break;
        }

        default:
        {
            /* No valid state, go to safe stop mode */
            eSystemMode = SYS_SAFESTOP;
        }
    }
}

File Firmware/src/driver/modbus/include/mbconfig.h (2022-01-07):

/*
 * FreeModbus Libary: A portable Modbus implementation for Modbus ASCII/RTU.
 * Copyright (c) 2006 Christian Walter <wolti@sil.at>
 * All rights reserved.
 *
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
 * File: $Id: mbconfig.h,v 1.15 2010/06/06 13:54:40 wolti Exp $
 */

#ifndef _MB_CONFIG_H
#define _MB_CONFIG_H

#ifdef __cplusplus
PR_BEGIN_EXTERN_C
#endif
/* ----------------------- Defines ------------------------------------------*/
/*! \defgroup modbus_cfg Modbus Configuration
 *
 * Most modules in the protocol stack are completly optional and can be
 * excluded. This is specially important if target resources are very small
 * and program memory space should be saved.<br>
 *
 * All of these settings are available in the file <code>mbconfig.h</code>
 *
 * Set XXX_ENABLED to value 1 will enable compilation of the related
 * part of codes.
 * And vice versa, to disable it set its value to 0.
 */
/*! \addtogroup modbus_cfg
 *  @{
 */
/*! \brief If Modbus ASCII support is enabled. */
#ifndef MB_ASCII_ENABLED
#define MB_ASCII_ENABLED                        ( 0)
#endif

/*! \brief If Modbus RTU support is enabled. */
#ifndef MB_RTU_ENABLED
#define MB_RTU_ENABLED                          ( 1)
#endif

/*! \brief If Modbus TCP support is enabled. */
#ifndef MB_TCP_ENABLED
#define MB_TCP_ENABLED                          ( 0)
#endif

/*! \brief The character timeout value for Modbus ASCII.
 *
 * The character timeout value is not fixed for Modbus ASCII and is therefore
 * a configuration option. It should be set to the maximum expected delay
 * time of the network.
 */
#ifndef MB_ASCII_TIMEOUT_SEC
#define MB_ASCII_TIMEOUT_SEC                    ( 1)
#endif

/*! \brief Timeout to wait in ASCII prior to enabling transmitter.
 *
 * If defined the function calls vMBPortSerialDelay with the argument
 * MB_ASCII_TIMEOUT_WAIT_BEFORE_SEND_MS to allow for a delay before
 * the serial transmitter is enabled. This is required because some
 * targets are so fast that there is no time between receiving and
 * transmitting the frame. If the master is to slow with enabling its
 * receiver then he will not receive the response correctly.
 */
#ifndef MB_ASCII_TIMEOUT_WAIT_BEFORE_SEND_MS
#define MB_ASCII_TIMEOUT_WAIT_BEFORE_SEND_MS    ( 0)
#endif

/*! \brief Maximum number of Modbus functions codes the protocol stack
 *    should support.
 *
 * The maximum number of supported Modbus functions must be greater than
 * the sum of all enabled functions in this file and custom function
 * handlers. If set to small adding more functions will fail.
 */
#ifndef MB_FUNC_HANDLERS_MAX
#define MB_FUNC_HANDLERS_MAX                    (16)
#endif

/*! \brief Number of bytes which should be allocated for the <em>Report Slave ID
 *    </em>command.
 *
 * This number limits the maximum size of the additional segment in the
 * report slave id function. See eMBSetSlaveID() for more information on
 * how to set this value. It is only used if MB_FUNC_OTHER_REP_SLAVEID_ENABLED
 * is set to <code>1</code>.
 */
#ifndef MB_FUNC_OTHER_REP_SLAVEID_BUF
#define MB_FUNC_OTHER_REP_SLAVEID_BUF           (32)
#endif

/*! \brief If the <em>Report Slave ID</em> function should be enabled. */
#ifndef MB_FUNC_OTHER_REP_SLAVEID_ENABLED
#define MB_FUNC_OTHER_REP_SLAVEID_ENABLED       ( 1)
#endif

/*! \brief If the <em>Read Input Registers</em> function should be enabled. */
#ifndef MB_FUNC_READ_INPUT_ENABLED
#define MB_FUNC_READ_INPUT_ENABLED              ( 1)
#endif

/*! \brief If the <em>Read Holding Registers</em> function should be enabled. */
#ifndef MB_FUNC_READ_HOLDING_ENABLED
#define MB_FUNC_READ_HOLDING_ENABLED            ( 1)
#endif

/*! \brief If the <em>Write Single Register</em> function should be enabled. */
#ifndef MB_FUNC_WRITE_HOLDING_ENABLED
#define MB_FUNC_WRITE_HOLDING_ENABLED           ( 1)
#endif

/*! \brief If the <em>Write Multiple registers</em> function should be enabled. */
#ifndef MB_FUNC_WRITE_MULTIPLE_HOLDING_ENABLED
#define MB_FUNC_WRITE_MULTIPLE_HOLDING_ENABLED  ( 1)
#endif

/*! \brief If the <em>Read Coils</em> function should be enabled. */
#ifndef MB_FUNC_READ_COILS_ENABLED
#define MB_FUNC_READ_COILS_ENABLED              ( 1)
#endif

/*! \brief If the <em>Write Coils</em> function should be enabled. */
#ifndef MB_FUNC_WRITE_COIL_ENABLED
#define MB_FUNC_WRITE_COIL_ENABLED              ( 1)
#endif

/*! \brief If the <em>Write Multiple Coils</em> function should be enabled. */
#ifndef MB_FUNC_WRITE_MULTIPLE_COILS_ENABLED
#define MB_FUNC_WRITE_MULTIPLE_COILS_ENABLED    ( 1)
#endif

/*! \brief If the <em>Read Discrete Inputs</em> function should be enabled. */
#ifndef MB_FUNC_READ_DISCRETE_INPUTS_ENABLED
#define MB_FUNC_READ_DISCRETE_INPUTS_ENABLED    ( 1)
#endif

/*! \brief If the <em>Read/Write Multiple Registers</em> function should be enabled. */
#ifndef MB_FUNC_READWRITE_HOLDING_ENABLED
#define MB_FUNC_READWRITE_HOLDING_ENABLED       ( 1)
#endif
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

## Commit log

2022-01-07 First release 1.0.0
    [PARTS.xlsx, sc.brd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]
2022-01-07 Release 1.1.0
    [PARTS.xlsx, SCX3.brd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]
2022-01-07 Release 1.2.0
    [SCX3.brd, SCX3.sch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]
